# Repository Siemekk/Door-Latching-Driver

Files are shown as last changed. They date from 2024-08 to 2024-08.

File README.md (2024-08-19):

# Door-Latching-Driver
Special driver for implementing the Soft Close system known from Audi, for other VAG group brands.

## PCB
PCB was full designed by my. Includes new automotive sockets for being more similar to full-comercial projects.
Program is being loaded by special ISP socket for programing. Dimension of PCB is ~62x49mm, so you can easliy put in inside Car.
PCB can be expanded to next options (For Example, closing mirrors after close Car), but I don't wanna do it, because all Cars after 2008 year, have this option in standard.

## Tests
Tests in old car (Audi A6 4F - 2006 year), was passed exactly! All things works like a new Car from 2022 year! The current consumption in sleep mode is less than <1mA, so battery is protected.
Breaking a process of latching door did not crash driver, driver wait for "full open door", and after that tries to latch it again!
In situation, where door "bowdeen cable" is broken, driver tries to latch door, but when status of door is not changed to "CLOSE", driver wait's for Open Doors, but don't REVERSE ENGINE. it's a sign to the user that something is wrong

## Assembly Instruction (Current in Polish)


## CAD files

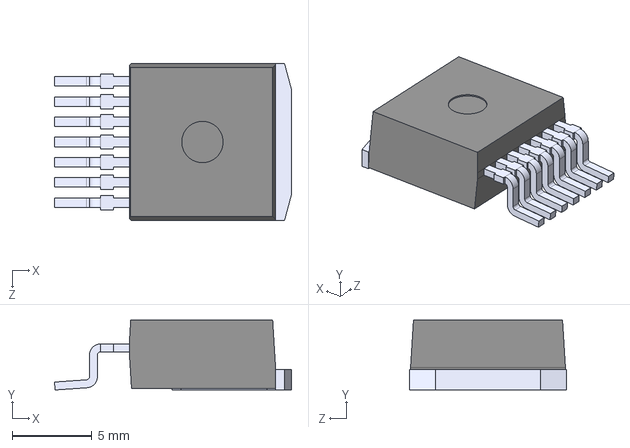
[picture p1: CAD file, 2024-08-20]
PCB/Footprints/BTS7960B/BTS7960B.step
14.9 x 4.40 x 9.90 mm

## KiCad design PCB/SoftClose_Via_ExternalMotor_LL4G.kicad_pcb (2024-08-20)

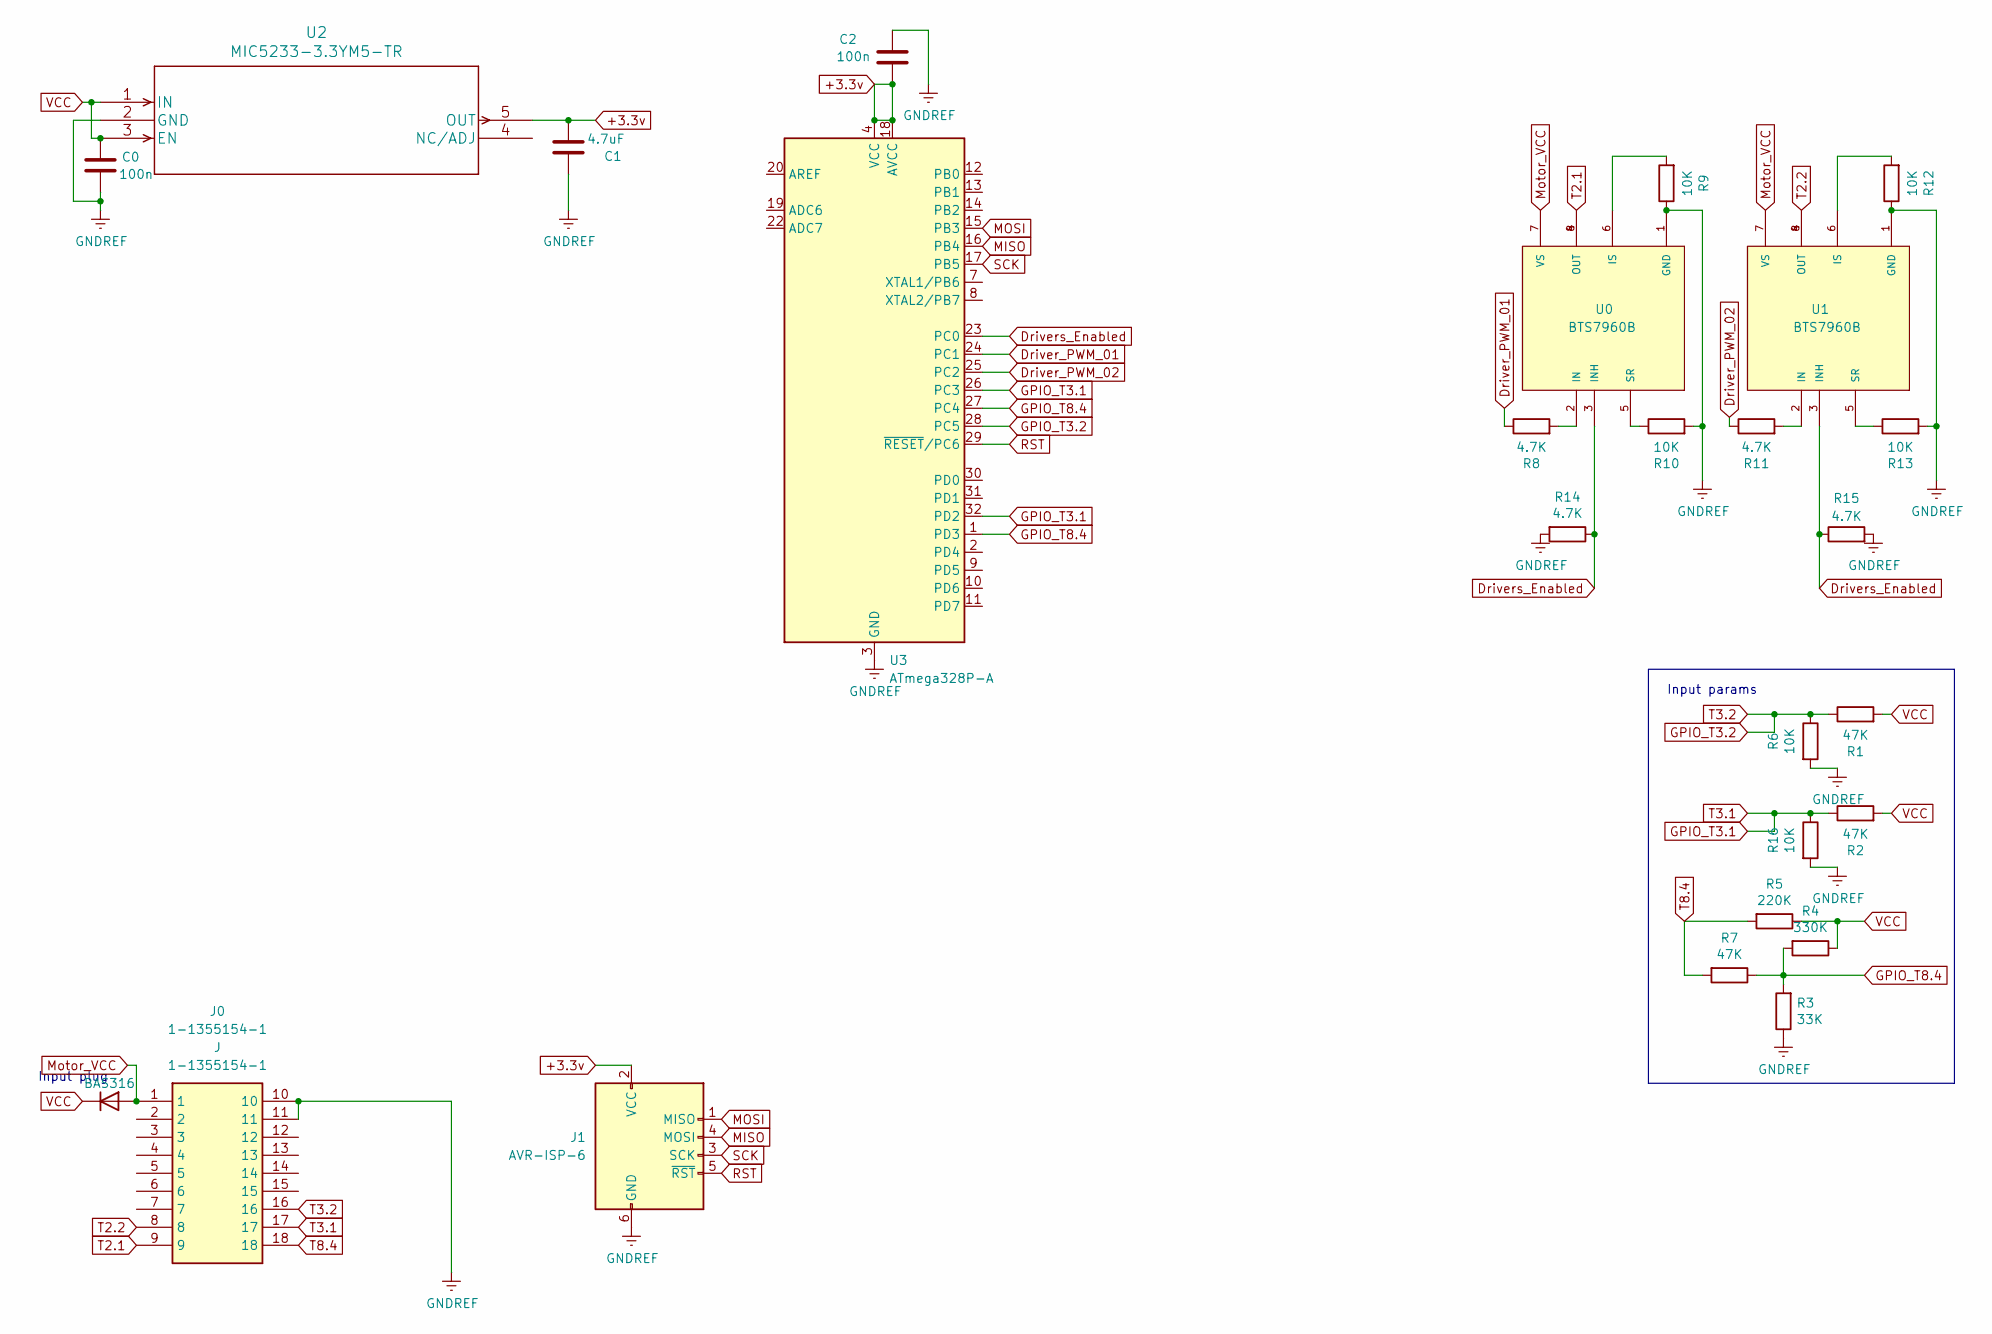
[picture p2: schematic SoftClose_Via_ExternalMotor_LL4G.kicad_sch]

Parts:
C0, C2: 100n; C_0603_1608Metric
C1: 4.7uF; C_0603_1608Metric
D0: BAS316; D_SOD-323
J0: 1-1355154-1; 113551541; Manufacturer_Part_Number 1-1355154-1; Mouser Part Number 571-1-1355154-1
J1: AVR-ISP-6; PinHeader_2x03_P2.54mm_Vertical
R1, R2, R7: 47K; R_0603_1608Metric
R3: 33K; R_0603_1608Metric
R4: 330K; R_0603_1608Metric
R5: 220K; R_0603_1608Metric
R6, R9, R10, R12, R13, R16: 10K; R_0603_1608Metric
R8, R11, R14, R15: 4.7K; R_0603_1608Metric
U0, U1: BTS7960B; DPAK127P1490X440-8N; PARTREV 1.1
U2: MIC5233-3.3YM5-TR
U3: ATmega328P-A; TQFP-32_7x7mm_P0.8mm

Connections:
+3.3v: C1.2, C2.2, J1.2 (VCC), U2.5 (OUT), U3.4 (VCC), U3.6 (VCC), U3.18 (AVCC)
Driver_PWM_01: R8.1, U3.24 (PC1)
Driver_PWM_02: R11.1, U3.25 (PC2)
Drivers_Enabled: R14.1, R15.1, U0.3 (INH), U1.3 (INH), U3.23 (PC0)
GPIO_T3.1: J0.17, R2.1, R16.1, U3.26 (PC3), U3.32 (PD2)
GPIO_T3.2: J0.16, R1.1, R6.1, U3.28 (PC5)
GPIO_T8.4: R3.2, R4.2, R7.1, U3.1 (PD3), U3.27 (PC4)
MISO: J1.4 (MOSI), U3.16 (PB4)
MOSI: J1.1 (MISO), U3.15 (PB3)
Motor_VCC: D0.2 (A), J0.1, U0.7 (VS), U1.7 (VS)
unnamed: R8.2, U0.2 (IN)
unnamed: R9.2, U0.6 (IS)
unnamed: R10.1, U0.5 (SR)
unnamed: R11.2, U1.2 (IN)
unnamed: R12.2, U1.6 (IS)
unnamed: R13.1, U1.5 (SR)
RST: J1.5 (~RST), U3.29 (~RESET/PC6)
SCK: J1.3 (SCK), U3.17 (PB5)
T2.1: J0.9, U0.4 (OUT), U0.8 (OUT)
T2.2: J0.8, U1.4 (OUT), U1.8 (OUT)
T8.4: J0.18, R5.2, R7.2
VCC: C0.1, D0.1 (K), R1.2, R2.2, R4.1, R5.1, U2.1 (IN), U2.3 (EN)

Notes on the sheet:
Input params
Input plug

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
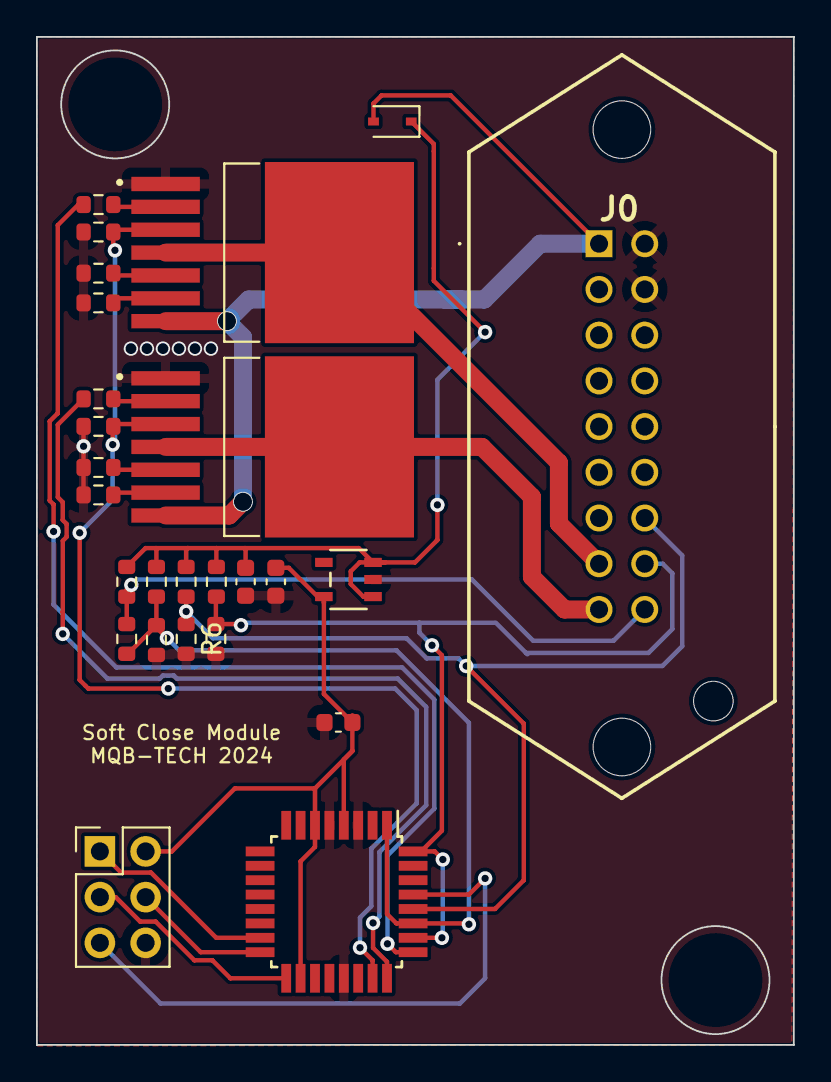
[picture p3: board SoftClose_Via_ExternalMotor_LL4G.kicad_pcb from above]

Board: 2 copper layers, 42.0 x 56.0 mm, 26 parts (0 on the bottom side), 23 nets.

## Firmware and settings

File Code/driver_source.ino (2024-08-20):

#include <avr/wdt.h>
#include <avr/interrupt.h>
#include <avr/sleep.h>

// Analog pins, for motor driver
#define PIN_MOSFET_ON 14
#define PIN_MOTOR_R   15
#define PIN_MOTOR_L   16

// GPIO PINS, from CAR and lock
#define PIN_T3_1 17
#define PIN_T3_2 19
#define PIN_T8_4 18

// MOTOR STATUS variables
const int STOP = 0;
const int FORWARD = 1;
const int REVERSE = 2;

// Time step for all process
const int checkDoorsClose_step  = 5;
const int doorLatching_step     = 12;

// Timer variables
unsigned long currentTime           = 0;
unsigned long savedTime_main        = 0;
unsigned long savedTime_checkSleep  = 0;
unsigned long checkSleepTime        = 7500UL;

// Variables with limit switches values
int status_PIN_3_1; 
int status_PIN_3_2;
int status_PIN_8_4;

// Counters, and fixes - for example, if user close doors fast, latching is not necessary.
// Other examples, on latching process (75% closed, switches return's 0, so it's necessary to chceck it with some delay)
int doorLatchingCounter;
int counterCheckDoorsClose;
bool emergencyLockProblem; 
bool lastChanceBeforeSleep;
void setup() 
{
  // Define motor driver as OUTPUT
  pinMode(PIN_MOSFET_ON, OUTPUT);
  pinMode(PIN_MOTOR_L, OUTPUT);
  pinMode(PIN_MOTOR_R, OUTPUT);
  
  // Define input pins
  pinMode(PIN_T3_1, INPUT);
  pinMode(PIN_T3_2, INPUT);
  pinMode(PIN_T8_4, INPUT);

  // Init Counters
  counterCheckDoorsClose = checkDoorsClose_step;
  doorLatchingCounter     = 0;
  emergencyLockProblem    = false;
  lastChanceBeforeSleep   = false;
}

// Like as function name
void readLimitSwitches()
{
  status_PIN_3_1 = digitalRead(PIN_T3_1);
  status_PIN_3_2 = digitalRead(PIN_T3_2);
  status_PIN_8_4 = digitalRead(PIN_T8_4);
}

// This function is used to run and stop motor
void setMotorState(int state)
{
  if (state == STOP)
  {
    analogWrite(PIN_MOSFET_ON, 0);
    analogWrite(PIN_MOTOR_L, 0);
    analogWrite(PIN_MOTOR_R, 0); 
    return; 
  }

  analogWrite(PIN_MOSFET_ON, 255);
  if(state == FORWARD)
  {
    analogWrite(PIN_MOTOR_L, 255);
    analogWrite(PIN_MOTOR_R, 0);  
  }
  else
  {
    analogWrite(PIN_MOTOR_L, 0);
    analogWrite(PIN_MOTOR_R, 255); 
  }
}
// This function setting module to sleep mode, it's very important, because module w/o sleep consumpt 12mA, so it ~50mA in all 4 doors!
// With this function module consumt 0.8mA at sleep mode
void sleepModule()
{
    static byte prevADCSRA = ADCSRA;
    ADCSRA = 0;
    set_sleep_mode (SLEEP_MODE_PWR_DOWN);
    sleep_enable();
    MCUCR = bit (BODS) | bit (BODSE);
    MCUCR = bit (BODS);
    
    noInterrupts();
    attachInterrupt(0, wakeUp, CHANGE);

    // Allow interrupts now
    interrupts();

    // And enter sleep mode as set above
    sleep_cpu();

    // Re-enable ADC if it was previously running
    ADCSRA = prevADCSRA;
}

// This function is called, when module going to wakeUP
void wakeUp()
{
  // Reinit Counters
  doorLatchingCounter = 0;
  counterCheckDoorsClose = checkDoorsClose_step;
  lastChanceBeforeSleep = false;
  detachInterrupt(0);
  
  delay(10);
}

// This function calls sleep
void doCheckSleep()
{
   if(analogRead(PIN_MOSFET_ON) > 0) 
   {
    // NEVER go sleep when, any motor is ON!
    return;
   }
   
   readLimitSwitches(); 
   if((status_PIN_3_1 == HIGH) && (status_PIN_8_4 == LOW))
   {
      if(!lastChanceBeforeSleep)
      { 
        lastChanceBeforeSleep = true;
        return;
      }
   }
   
   lastChanceBeforeSleep = false; 
   setMotorState  (STOP); // Stop motors!
   sleepModule    ();     // Go sleep!
}

// Main process for motor forward STATE
void processLatching()
{
  if(!doorLatchingCounter) doorLatchingCounter = doorLatching_step;
  setMotorState(FORWARD); 
  doorLatchingCounter--;
  if(doorLatchingCounter <= 0)
  {
    if(status_PIN_8_4 == LOW)
    {
      // Some troubles with latching - setting to emergency mode
      emergencyLockProblem = true;
    } 
  }
}

// POST method for reset counters, and reverse motor!
void processReverse()
{
   if(status_PIN_3_2 == LOW)
        setMotorState(REVERSE);
   else setMotorState(STOP);

   // Reset counters
   doorLatchingCounter        = 0;
   counterCheckDoorsClose  = checkDoorsClose_step;
}

// Main process for door
void processDoor()
{
  readLimitSwitches();

  if(status_PIN_3_1 == LOW && !doorLatchingCounter)
  { 
    processReverse();
    emergencyLockProblem    = false;
  }
  else
  {
    if((status_PIN_8_4 == LOW || doorLatchingCounter) && !emergencyLockProblem)
    {  
      if(counterCheckDoorsClose > 0)  counterCheckDoorsClose--;
      else                            processLatching();
    }
    else
      processReverse();
  }
}
// the loop function runs over and over again forever
void loop() 
{
  currentTime       = millis();
  if(currentTime -  savedTime_checkSleep >= checkSleepTime)  
  {
    savedTime_checkSleep = currentTime;
    doCheckSleep();
  } 
  
  if(currentTime - savedTime_main >= 50UL)
  {
    savedTime_main = currentTime; 
    processDoor();
  } 
}

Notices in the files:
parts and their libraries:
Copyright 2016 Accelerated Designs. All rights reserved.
